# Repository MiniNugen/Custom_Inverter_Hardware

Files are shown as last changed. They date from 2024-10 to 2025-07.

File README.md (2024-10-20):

# Custom_Inverter_Hardware
## File Tree Should be organized like so:

PCB_Project_Name_REV1.PrjPCB  
|  Source Documents  
|  |  PCB_Project_Name_REV1.SchDOC  
|  |  PCB_Project_Name_REV1.PcbDOC  
|  |  BOM  
|  Settings  
|  Libraries  

PCB_Project_Name_REV2.PrjPCB  
|  Source Documents  
|  |  PCB_Project_Name_REV2.SchDOC  
|  |  PCB_Project_Name_REV2.PcbDOC  
|  |  BOM  
|  Settings  
|  Libraries  

PCB_Project_Name_REV3.PrjPCB  
|  Source Documents  
|  |  PCB_Project_Name_REV3.SchDOC  
|  |  PCB_Project_Name_REV3.PcbDOC  
|  |  BOM  
|  Settings  
|  Libraries

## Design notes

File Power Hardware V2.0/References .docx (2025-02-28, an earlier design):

https://www.ti.com/lit/ug/tiducg2/tiducg2.pdf

^main gate design reference

Gate driver ic data shee (https://www.ti.com/lit/ds/symlink/drv8300.pdf)t

Mosfet data sheet (https://www.ti.com/lit/ds/symlink/csd19532q5b.pdf?HQS=dis-dk-null-digikeymode-dsf-pf-null-wwe&ts=1740251644852)

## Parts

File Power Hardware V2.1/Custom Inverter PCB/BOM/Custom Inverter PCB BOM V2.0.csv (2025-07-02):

Reference | Value | Datasheet | Footprint | Qty | DNP | Part Number
C1,C15 | 0.1uF | https://www.digikey.ca/en/products/detail/kyocera-avx/0805ZD104KAT2A/1603455 | Capacitor_SMD:C_0805_2012Metric | 2 |  | 0805ZD104KAT2A
C2 | 0.33uF | https://www.digikey.ca/en/products/detail/murata-electronics/GRM219R71H334KA88D/702591 | Capacitor_SMD:C_0805_2012Metric | 1 |  | GRM219R71H334KA88D
C3,C4,C5 | 1uF | https://www.digikey.ca/en/products/detail/samsung-electro-mechanics/CL21B105KBFNFNE/3891014 | Capacitor_SMD:C_0805_2012Metric | 3 |  | CL21B105KBFNFNE
C6,C7,C8 | 1uF | https://www.digikey.ca/en/products/detail/tdk-corporation/CGA6M2X7R2A105K200AA/2443343 | Capacitor_SMD:C_1210_3225Metric | 3 |  | CGA6M2X7R2A105K200AA
C9,C10 | 330 µF | https://industrial.panasonic.com/cdbs/www-data/pdf/RDE0000/ABA0000C1181.pdf | EEV_FK2A331M:CAP_EEVFK2A331M | 2 |  | EEVFK2A331M
C11,C12,C13,C14 | 220nF | ~ | Capacitor_SMD:C_0603_1608Metric | 4 |  | CL21B224KAFNNNE
C21,C23,C24 | 47nF |  | Capacitor_SMD:C_0805_2012Metric | 3 |  | C0805C473K5RACTU
C28 | 0.1uF | https://www.digikey.ca/en/products/detail/yageo/CC0805KRX7R9BB104/302874 | Capacitor_SMD:C_0805_2012Metric | 1 |  | CC0805KRX7R9BB104
CR1,CR2,CR3 | ~ | BAV20WS-TP | BAV20WS-TP:CR_SOD-323_MCC | 3 |  | BAV20WS-TP
CR4 | LD1085D2M33R |  | LD1085D2M33R:D2PAK&slash_A_STM | 1 |  | LD1085D2M33R
F1,F2,F3,F4 | 250V 30A | 0463030.ER | 0463030_ER:FUSE_0463_LTF-M | 4 |  | 0463030.ER
J1,J2,J7,J8 | 1714971 |  | 1714971:PHOENIX_1714971 | 4 |  | 1714971
J3 | 1714968 |  | PHOENIX_1714968:PHOENIX_1714968 | 1 |  | 1714968
J4,J5,J9,J10 | 10897202 | 10897202 | CONN20_0010897202_MOL | 4 |  | 10897202
J6 | 1989764 | ~ | PHOENIX_1989764:PHOENIX_1989764 | 1 |  | 1989764
K2 | 1-1393210-3 |  | T9AS1D12_12:TE_1-1393210-3 | 1 |  | T9AS1D12-12
Q1,Q2,Q3,Q4,Q5,Q6 | CSD19532Q5B |  | CSD19532Q5B:TRANS_CSD19532Q5B | 6 |  | CSD19532Q5B
R1,R2,R3,R4,R6,R7 | 15R | https://www.digikey.ca/en/products/detail/panasonic-electronic-components/ERJ-6GEYJ150V/82975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 | Resistor_SMD:R_0805_2012Metric | 6 |  | ERJ-6GEYJ150V
R5,R8,R9,R18 | 10k | https://industrial.panasonic.com/cdbs/www-data/pdf/RDM0000/AOA0000C307.pdf | Resistor_SMD:R_0805_2012Metric | 4 |  | ERA-6AEB103V
R10,R11,R12,R13,R14,R15,R16,R17 | 4.7K | ~ | Resistor_SMD:R_0805_2012Metric | 8 |  | CRCW08054K70FKEAC
R32,R35,R36 | 220R |  | Resistor_SMD:R_0805_2012Metric | 3 |  | CRGCQ0805F220R
R43 | 97.6K | https://www.digikey.ca/en/products/detail/yageo/RC0805FR-0797K6L/728213 | Resistor_SMD:R_0805_2012Metric | 1 |  | RC0805FR-0797K6L
R44,R45,R46,R47,R48 | 3K | https://www.digikey.ca/en/products/detail/te-connectivity-passive-product/CRG0805F3K0/2380900 | Resistor_SMD:R_0805_2012Metric | 5 |  | CRG0805F3K0
TP1,TP2,TP3,TP4,TP5,TP6,TP7,TP8,TP9 | 5002 |  | 5002:KEYSTONE_5002 | 9 |  | 5002
U1 | DRV8300DIPWR | DRV8300DIPWR | DRV8300DIPWR:TSSOP_0DIPWR_TEX | 1 |  | DRV8300DIPWR
U2,U3,U4 | TLI4971A050T5E0001XUMA1 | TLI4971A050T5E0001XUMA1 | TLI4971A:IC_TLI4971A050T5UE0001XUMA1 | 3 |  | TLI4971A050T5E0001XUMA1
U5 | LAUNCHXL-F280049C |  | LAUNCHXL-F280049C:MODULE_LAUNCHXL-F280049C | 1 |  | LAUNCHXL-F280049C
U6 | OP292GSZ-REEL | OP292GSZ-REEL | R_8_ADI | 1 |  | OP292GSZ-REEL

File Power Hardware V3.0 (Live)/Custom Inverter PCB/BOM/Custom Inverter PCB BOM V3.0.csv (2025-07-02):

Reference | Value | Datasheet | Footprint | Qty | DNP | Part Number
C1,C2 | 330 µF | https://industrial.panasonic.com/cdbs/www-data/pdf/RDE0000/ABA0000C1181.pdf | EEV_FK2A331M:CAP_EEVFK2A331M | 2 |  | EEVFK2A331M
C3 | 0.1uF | https://www.digikey.ca/en/products/detail/yageo/CC0805KRX7R9BB104/302874 | Capacitor_SMD:C_0805_2012Metric | 1 |  | CC0805KRX7R9BB104
C4,C5,C6 | 1uF | https://www.digikey.ca/en/products/detail/samsung-electro-mechanics/CL21B105KBFNFNE/3891014 | Capacitor_SMD:C_0805_2012Metric | 3 |  | CL21B105KBFNFNE
C7,C8,C9 | 1uF | https://www.digikey.ca/en/products/detail/tdk-corporation/CGA6M2X7R2A105K200AA/2443343 | Capacitor_SMD:C_1210_3225Metric | 3 |  | CGA6M2X7R2A105K200AA
C10,C11,C12,C13,C27 | 220nF | ~ | Capacitor_SMD:C_0603_1608Metric | 5 |  | CL21B224KAFNNNE
C14,C15,C16 | 47nF |  | Capacitor_SMD:C_0805_2012Metric | 3 |  | C0805C473K5RACTU
C17,C24,C25 | 0.1uF | https://www.digikey.ca/en/products/detail/kyocera-avx/0805ZD104KAT2A/1603455 | Capacitor_SMD:C_0805_2012Metric | 3 |  | 0805ZD104KAT2A
C19,C20 | 0.33uF | https://www.digikey.ca/en/products/detail/murata-electronics/GRM219R71H334KA88D/702591 | Capacitor_SMD:C_0805_2012Metric | 2 |  | GRM219R71H334KA88D
CR1,CR2,CR3 | ~ | BAV20WS-TP | BAV20WS-TP:CR_SOD-323_MCC | 3 |  | BAV20WS-TP
CR4 | LD1085D2M33R | https://www.st.com/content/ccc/resource/technical/document/datasheet/d3/84/d5/f6/3c/23/40/7b/CD00001883.pdf/files/CD00001883.pdf/jcr:content/translations/en.C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 | LD1085D2M33R:D2PAK&slash_A_STM | 1 |  | LD1085D2M33R
D10,D11,D12,D13,D14 | 100V IN,12V,3.3V,5V,BRIDGE ON | https://mm.digikey.com/Volume0/opasdata/d220001/medias/docus/3739/B1931UY--20D000114U1930.pdf | Capacitor_SMD:C_0603_1608Metric_Pad1.08x0.95mm_HandSolder | 5 |  | B1931UY--20D000114U1930
F1,F2,F3,F4 | 100VDC 50A,250VAC 50A | https://www.bourns.com/docs/Product-Datasheets/SF-3812F-T.pdf | 0463030_ER:FUSE_0463_LTF-M | 4 |  | SF-3812F5000T-2
J1,J8,J9 | 1990009 |  | 2P term 1990009:PHOENIX_1990009 | 3 |  | 1990009
J2,J3,J4,J5 | 10897202 | 10897202 | CONN20_0010897202_MOL | 4 |  | 10897202
J6,J10,J11 | 1990041 |  | PHOENIX_1990041:PHOENIX_1990041 | 3 |  | 1990041
J7 | 1714971 |  | 1714971:PHOENIX_1714971 | 1 |  | 1714971
K1 | 1-1393210-3 | https://www.te.com/en/product-1-1393210-3.datasheet.pdf | T9AS1D12_12:TE_1-1393210-3 | 1 |  | 1-1393210-3
MP1,MP2,MP3,MP4,MP5 | 7461383 | 7461383 | M5 Screw Term 7461383:WP-SHFU_7461383 | 5 |  | 7461383
Q1,Q2,Q3,Q4,Q5,Q6 | IRFB4115PBF | https://www.infineon.com/dgdl/irfb4115pbf.pdf?fileId=5546d462533600a401535615ba6a1e0f | Package_TO_SOT_THT:TO-220-3_Vertical | 6 |  | IRFB4115PBF
R1 | 97.6K | https://www.digikey.ca/en/products/detail/yageo/RC0805FR-0797K6L/728213 | Resistor_SMD:R_0805_2012Metric | 1 |  | RC0805FR-0797K6L
R2,R22,R23,R26,R28 | 3K | https://www.digikey.ca/en/products/detail/te-connectivity-passive-product/CRG0805F3K0/2380900 | Resistor_SMD:R_0805_2012Metric | 5 |  | CRG0805F3K0
R3,R4,R5,R6,R7,R8 | 15R | https://www.digikey.ca/en/products/detail/panasonic-electronic-components/ERJ-6GEYJ150V/82975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 | Resistor_SMD:R_0805_2012Metric | 6 |  | ERJ-6GEYJ150V
R9,R10,R11,R12,R13,R14,R15,R16 | 4.7K | ~ | Resistor_SMD:R_0805_2012Metric | 8 |  | CRCW08054K70FKEAC
R17,R18,R19,R33,R34,R35,R36,R37 | 220R | CRGCQ0805F220R | Resistor_SMD:R_0805_2012Metric | 8 |  | CRGCQ0805F220R
R20 | 5.36k | https://www.yageo.com/upload/media/product/products/datasheet/rchip/PYu-RC_Group_51_RoHS_L_12.pdf | Resistor_SMD:R_0805_2012Metric | 1 |  | RC0805FR-075K36L
R21,R24,R25,R27 | 10k | https://industrial.panasonic.com/cdbs/www-data/pdf/RDM0000/AOA0000C307.pdf | Resistor_SMD:R_0805_2012Metric | 4 |  | ERA-6AEB103V
R49,R50,R51,R52 | 2.7k | https://industrial.panasonic.com/cdbs/www-data/pdf/RDO0000/AOA0000C331.pdf | Resistor_SMD:R_0805_2012Metric | 4 |  | ERJ-P06J272V
TP1,TP2,TP3,TP4,TP5,TP6,TP7,TP8,TP9 | 5002 |  | 5002:KEYSTONE_5002 | 9 |  | 5002
U1 | DRV8300DIPWR | https://www.ti.com/lit/ds/symlink/drv8300.pdf | DRV8300DIPWR:TSSOP_0DIPWR_TEX | 1 |  | DRV8300DIPWR
U2 | LAUNCHXL-F280049C | https://www.ti.com/lit/ug/spruii7b/spruii7b.pdf?ts=1748422871760 | LAUNCHXL-F280049C:MODULE_LAUNCHXL-F280049C | 1 |  | LAUNCHXL-F280049C
U3,U4,U5 | TLI4971A050T5E0001XUMA1 | https://www.infineon.com/dgdl/Infineon-TLI4971_25_50_75_120-DataSheet-v01_20-EN.pdf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 | TLI4971A:TLI4971A050T5UE0001XUMA1 | 3 |  | TLI4971A050T5E0001XUMA1
U6 | OP292GSZ-REEL | https://www.analog.com/media/en/technical-documentation/data-sheets/OP292_492.pdf | R_8_ADI | 1 |  | OP292GSZ-REEL
U7 | L78M05CDT-TR | L78M05CDT-TR | L78M05CDT_TR:DPAK_STM-M | 1 |  | L78M05CDT-TR

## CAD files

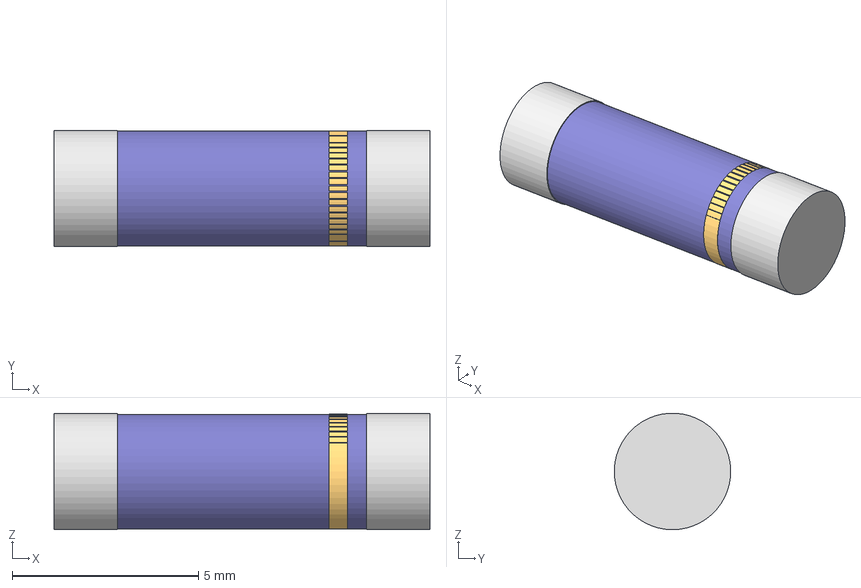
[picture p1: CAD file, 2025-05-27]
Power Hardware V3.0 (Live)/Custom Inverter PCB/EDA Models/0463030_ER/FUSE_0463_LTF.step
10.1 x 3.12 x 3.12 mm

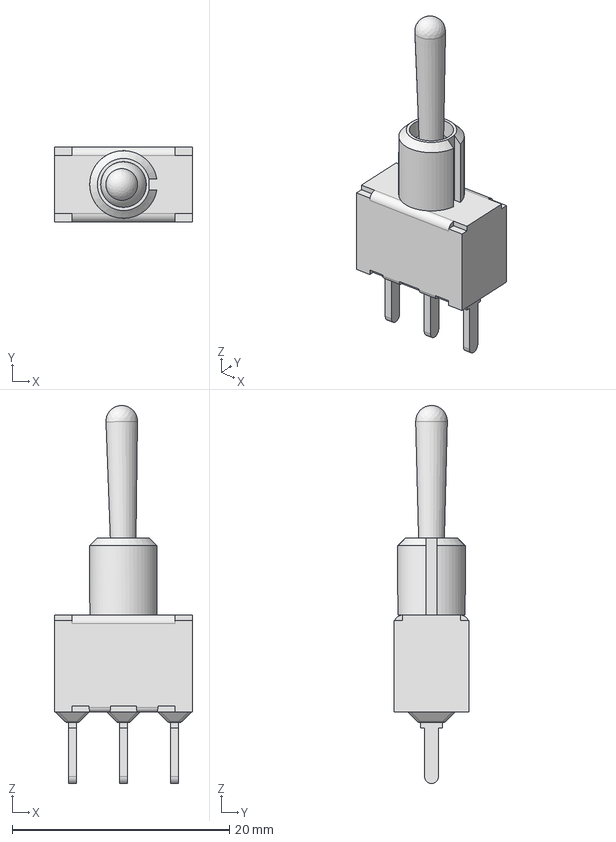
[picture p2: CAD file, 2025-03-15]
Power Hardware V3.0 (Live)/Custom Inverter PCB/EDA Models/100SP1T1B4M2QE/100SP1T1B4M2QE.step
12.7 x 6.86 x 34.8 mm

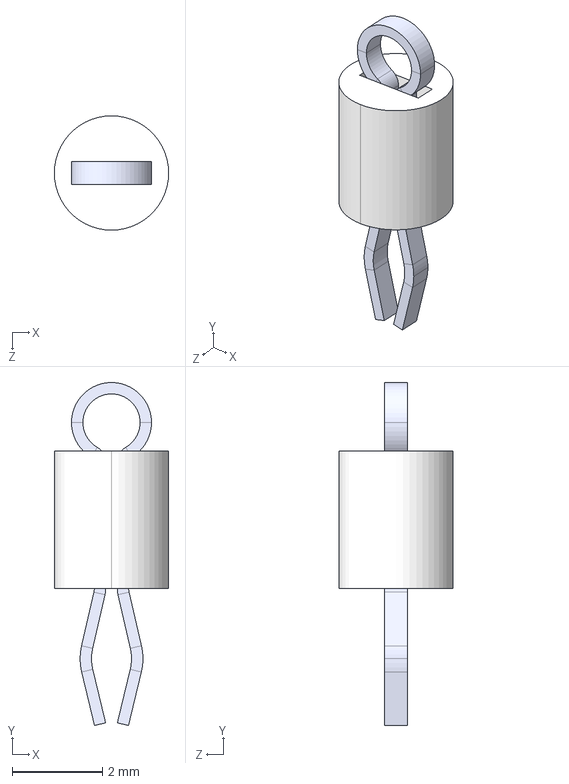
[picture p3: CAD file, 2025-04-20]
Power Hardware V3.0 (Live)/Custom Inverter PCB/EDA Models/5002/5002.step
2.54 x 7.62 x 2.54 mm

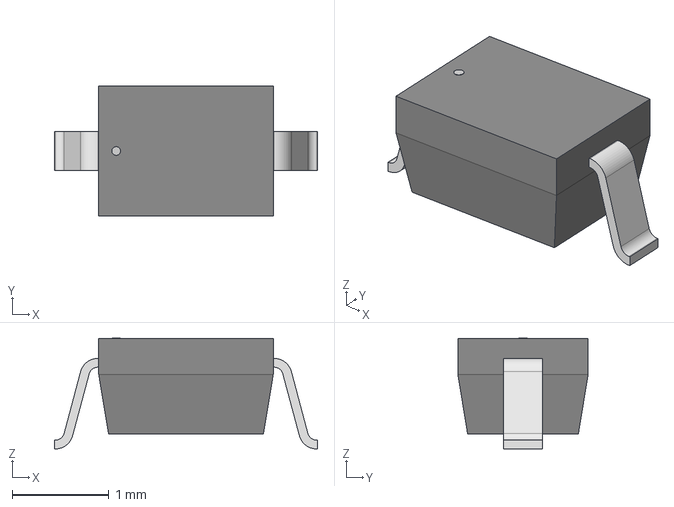
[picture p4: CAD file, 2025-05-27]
Power Hardware V3.0 (Live)/Custom Inverter PCB/EDA Models/BAV20WS_TP/CR_SOD-323_MCC.step
2.72 x 1.35 x 1.15 mm

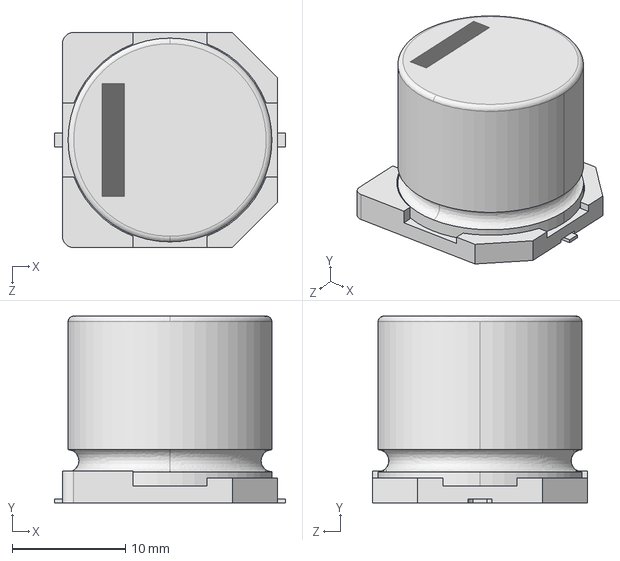
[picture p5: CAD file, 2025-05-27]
Power Hardware V3.0 (Live)/Custom Inverter PCB/EDA Models/EEV_FK2A331M/EEVFK2A331M.step
20.4 x 16.5 x 19.0 mm

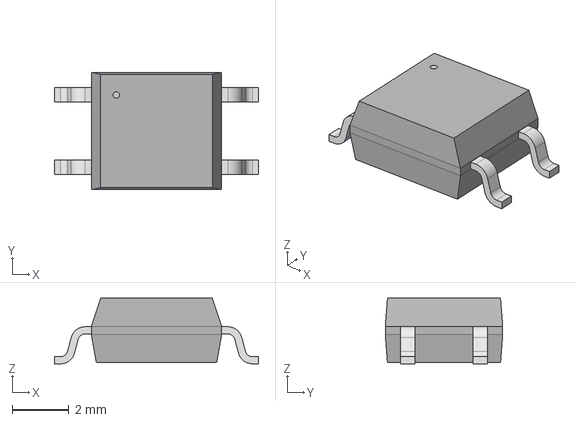
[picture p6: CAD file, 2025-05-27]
Power Hardware V3.0 (Live)/Custom Inverter PCB/EDA Models/HCPL_181_06BE/HCPL-181_BRA.step
7.19 x 4.14 x 2.31 mm

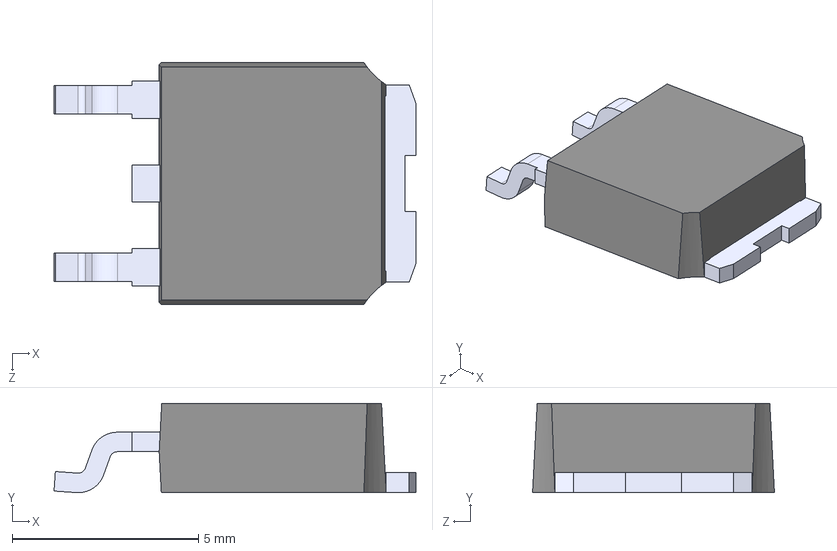
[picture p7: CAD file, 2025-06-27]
Power Hardware V3.0 (Live)/Custom Inverter PCB/EDA Models/L78M05CDT_TR/L78M05CDT-TR.step
9.72 x 2.40 x 6.50 mm

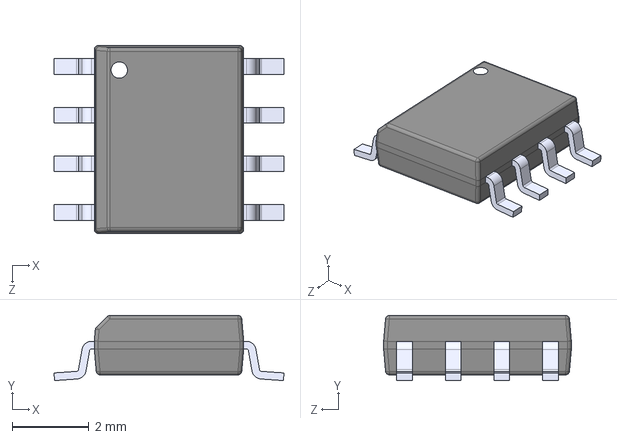
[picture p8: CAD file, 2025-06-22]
Power Hardware V3.0 (Live)/Custom Inverter PCB/EDA Models/LM5164DDAT/LM5164DDAT.step
6.00 x 1.70 x 4.90 mm

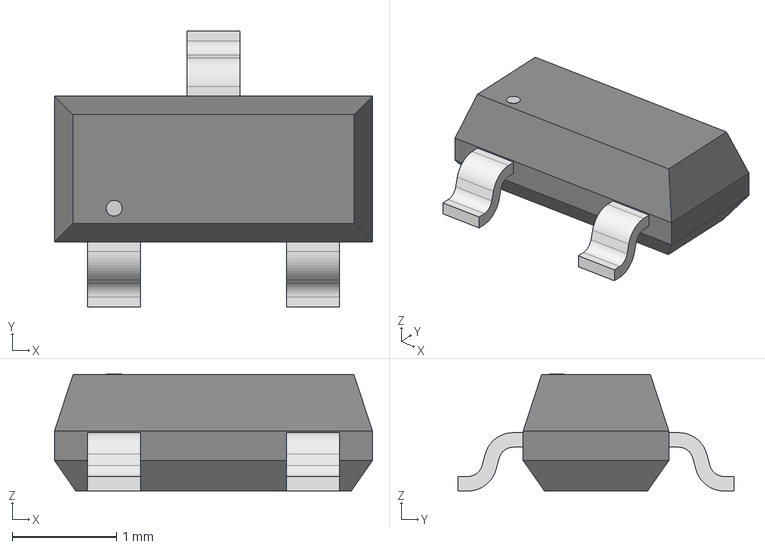
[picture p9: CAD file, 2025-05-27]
Power Hardware V3.0 (Live)/Custom Inverter PCB/EDA Models/NTR4170NT1G/SOT-23_ONS.step
3.05 x 2.64 x 1.12 mm

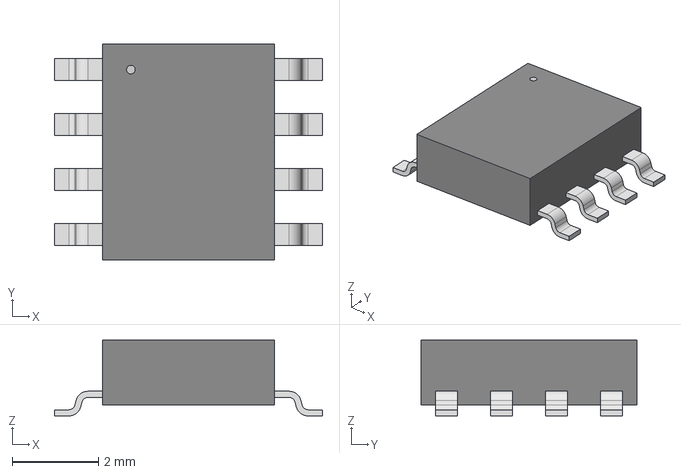
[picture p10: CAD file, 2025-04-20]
Power Hardware V3.0 (Live)/Custom Inverter PCB/EDA Models/OP292GSZ-REEL/OP292GSZ-REEL.step
6.20 x 5.00 x 1.75 mm

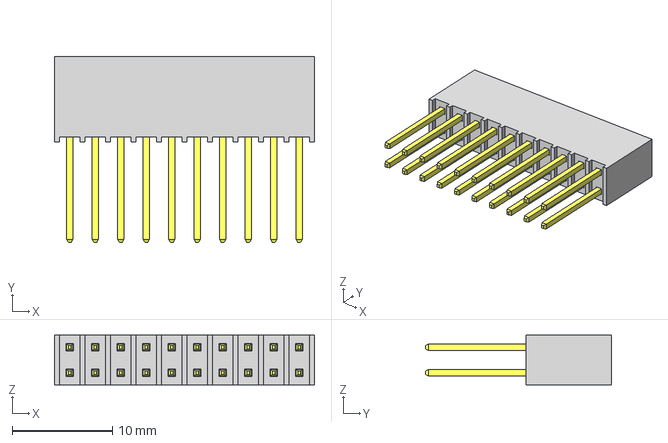
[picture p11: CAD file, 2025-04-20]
Power Hardware V3.0 (Live)/Custom Inverter PCB/EDA Models/SSQ_110_03_G_D/SSQ-110-03-G-D.step
25.9 x 18.5 x 4.95 mm
T1SSQ-110-03-G-D
P2SSQ-110-03-G-D

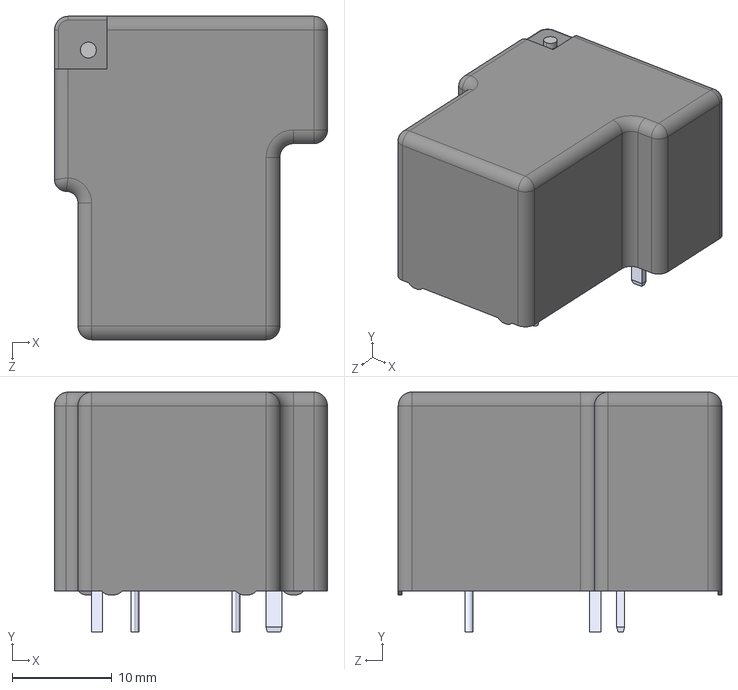
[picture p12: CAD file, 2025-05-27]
Power Hardware V3.0 (Live)/Custom Inverter PCB/EDA Models/T9AS1D12_12/1-1393210-3.step
27.4 x 24.1 x 32.5 mm

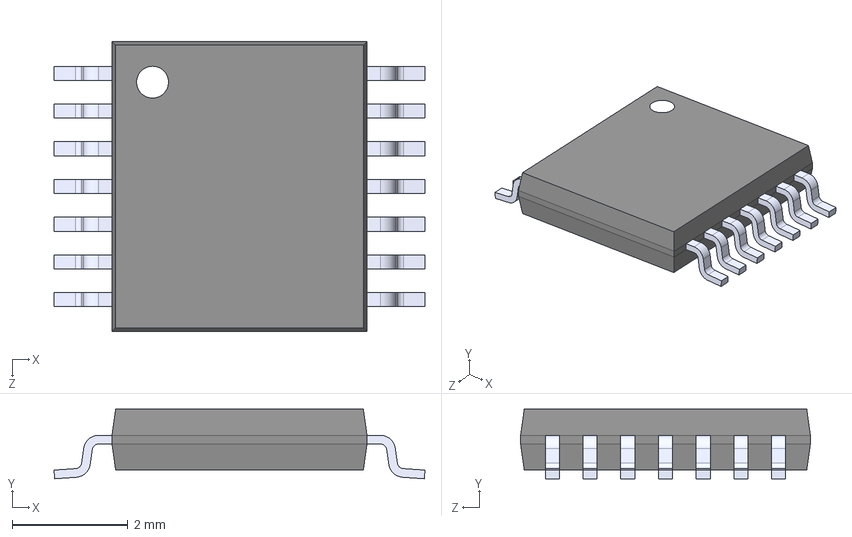
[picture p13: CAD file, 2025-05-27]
Power Hardware V3.0 (Live)/Custom Inverter PCB/EDA Models/TLV9004IPWR/TLV9004IPWR.step
6.40 x 1.20 x 5.00 mm

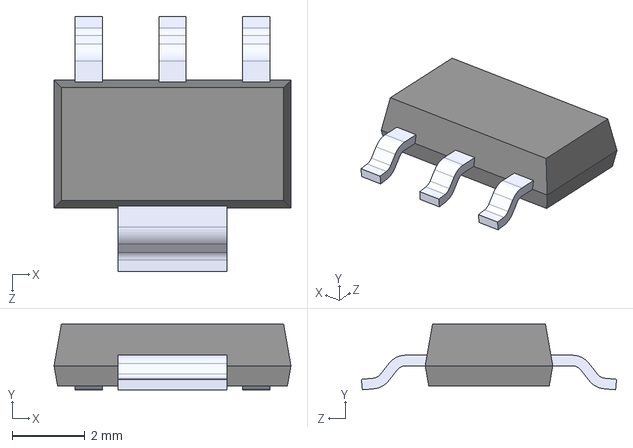
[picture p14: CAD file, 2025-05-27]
Power Hardware V3.0 (Live)/Custom Inverter PCB/EDA Models/UA78M33CDCYR/UA78M33CDCYR.step
6.50 x 1.80 x 7.00 mm

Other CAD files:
Power Hardware V3.0 (Live)/Custom Inverter PCB/EDA Models/1935161/1935161.step
Power Hardware V3.0 (Live)/Custom Inverter PCB/EDA Models/1989764/1989764.step
Power Hardware V3.0 (Live)/Custom Inverter PCB/EDA Models/1990041/1990041.step
Power Hardware V3.0 (Live)/Custom Inverter PCB/EDA Models/CSD19532Q5B/CSD19532Q5B.step
Power Hardware V2.0/LAUNCHXL-F280049C - ALTIUM/RevB/MCU025B_design_files/ALTIUM_EMBEDDED_MODELS/1051640001.stp
Power Hardware V2.0/LAUNCHXL-F280049C - ALTIUM/RevB/MCU025B_design_files/ALTIUM_EMBEDDED_MODELS/60900213421.stp
Power Hardware V2.0/LAUNCHXL-F280049C - ALTIUM/RevB/MCU025B_design_files/ALTIUM_EMBEDDED_MODELS/61300211121.stp
Power Hardware V2.0/LAUNCHXL-F280049C - ALTIUM/RevB/MCU025B_design_files/ALTIUM_EMBEDDED_MODELS/61300311121.stp
Power Hardware V2.0/LAUNCHXL-F280049C - ALTIUM/RevB/MCU025B_design_files/ALTIUM_EMBEDDED_MODELS/D0008A.stp
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

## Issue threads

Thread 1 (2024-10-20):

Select test motor that the inverter will be made to test

MiniNugen, 2024-10-20:
Decide on a motor so we can design our project around it.
Requirements:
- 3-Phase AC
- Permanent-magnet synchronous motor
- 60V to 120V AC voltage
- No larger than 8kW of power draw

Closed 2024-10-26.

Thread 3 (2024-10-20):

Simulate a 3-phase H Bridge + PWM current generator

MiniNugen, 2024-10-20:
A PWM controller is required to drive a 3-phase H-bridge setup. When done correctly, the output of each inverter phase should have a voltage level proportional to the duty cycle of the PWM controller.

[This model is what my our inverter will be based on. So read this if you need extra resources](https://uwin365-my.sharepoint.com/:b:/g/personal/nguyen39_uwindsor_ca/EXIsp8yUNkpArx_SbNmMhxcB7SE95WXn12xlHMAQ0pFSlA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)

TLDR: Here's the plan, we'll need  3 PWM controllers. One for each phase. They will each receive an analog signal input between 2 to 12V. A 2V signal means the PWM is getting requested to generate a 0% duty cycle wave and a 12V means the PWM is getting requested to generate a 100% duty cycle wave. The wave will have ____Hz frequency (We'll decide on a frequency after we've established a speed requirement).  These PWM signals will be used to drive a Transistor array. Then the PWM signal is at 0% duty cycle, we should expect to see 0V at the output of that H-Bridge phase, When the PWM signal is at 100%, we should see our Power voltage at the output.

When the Duty cycle is 0%, we would expect the overall voltage at that phase to be 0%

Josh-Levesque, 2024-10-22:
[This model is what my our inverter will be based on. So read this if you need extra resources](https://uwin365-my.sharepoint.com/:b:/r/personal/nguyen39_uwindsor_ca/Documents/%5BFULLTEXT01.pdf%5D(https://uwin365-my.sharepoint.com/:b:/r/personal/nguyen39_uwindsor_ca/Documents/FULLTEXT01.pdf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)?csf=1&web=1&e=icIfjU)

This link is broken

Closed 2024-10-26.

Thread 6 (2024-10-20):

First Iteration of controls circuit.

MiniNugen, 2024-10-20:
Design, the first Iteration of the control board.
Just a fast microprocessor that needs to work fast to keep up with calculating PARK and CLARKE conversions, track current data, receive Throttle inputs, and perform traction control. This also needs some built-in PI and PID controllers.

Closed 2025-01-09.

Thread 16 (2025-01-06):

Revision2 Hardware Design

MiniNugen, 2025-01-06:
Revision 2 is where the gate driver circuit and microcontroller circuit are put together into 1 PCB.
Some updates for this revision shoud include:
- replace all passive components smaller than 0603. This is to make manufacturing easier.
- Reduce the microcontroller board down to 4 layers
- Conjoin both gate driver board and micro controller circuit.
- Remove all unused GPIO connections

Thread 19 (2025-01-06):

Copy the current microcontroller and Gate Driver PCB into one shared altiumproject

MiniNugen, 2025-01-06:
After converting the microcontroller PCB from 6 layers to a 4-layer board, it shall be inspected and approved.
Copy the modified microcontroller and the latest Gate Driver PCB into one shared Altium project (file name: TI-C200 inverter V2)

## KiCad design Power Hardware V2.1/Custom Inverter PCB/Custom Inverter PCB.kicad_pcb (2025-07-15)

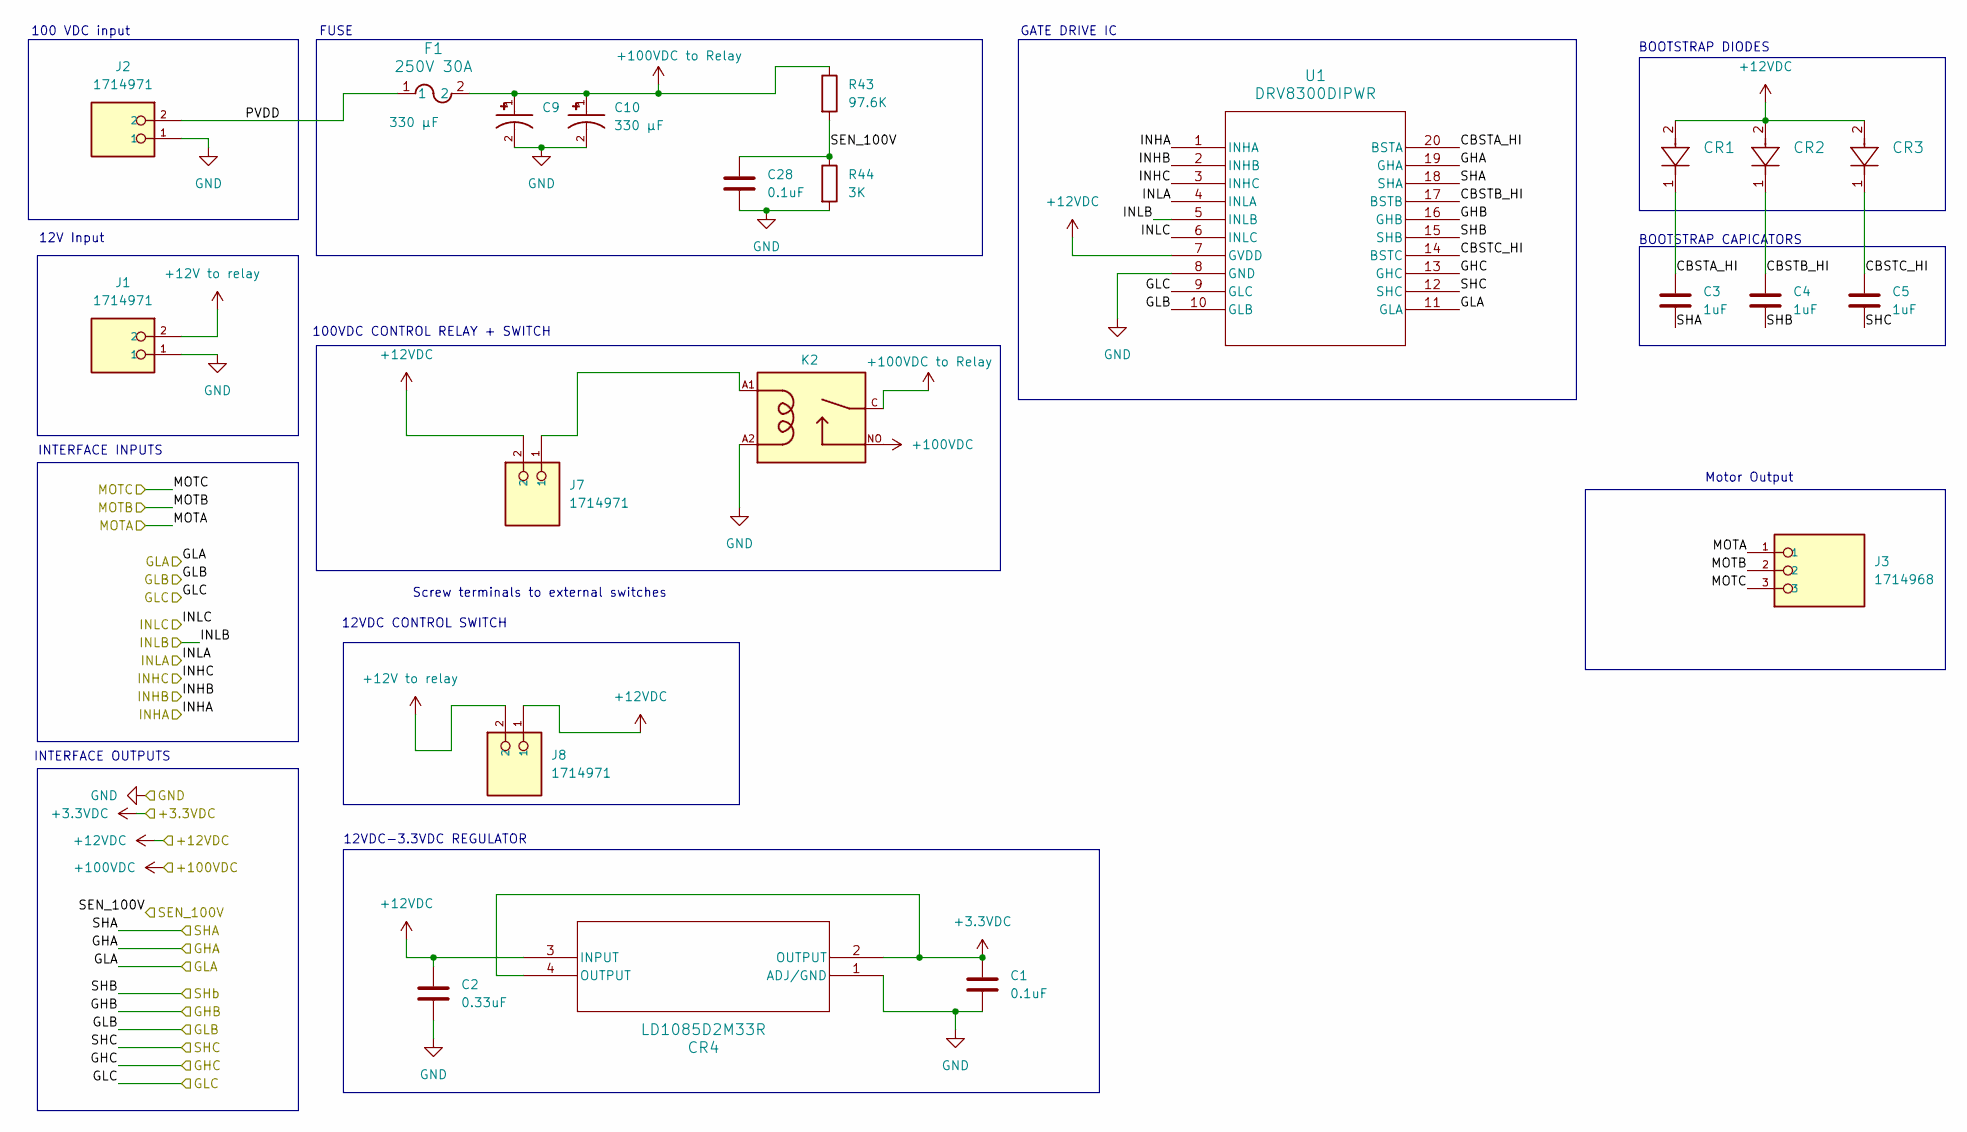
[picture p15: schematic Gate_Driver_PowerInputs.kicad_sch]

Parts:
C1: 0.1uF; C_0805_2012Metric; Part Number 0805ZD104KAT2A
C2: 0.33uF; C_0805_2012Metric; Part Number GRM219R71H334KA88D
C3, C4, C5: 1uF; C_0805_2012Metric; Part Number CL21B105KBFNFNE
C9, C10: 330 µF; CAP_EEVFK2A331M; PARTREV 10-Oct-19
C28: 0.1uF; C_0805_2012Metric; Part Number CC0805KRX7R9BB104
CR1, CR2, CR3: CR_SOD-323_MCC; Part Number BAV20WS-TP
CR4: LD1085D2M33R; D2PAK&slash_A_STM; Part Number LD1085D2M33R
F1: 250V 30A; FUSE_0463_LTF-M; Part Number 0463030.ER
J1, J2, J7, J8: 1714971; PHOENIX_1714971; PARTREV 26.05.2020
J3: 1714968; PHOENIX_1714968; Part Number 1714968
K2: 1-1393210-3; TE_1-1393210-3; PARTREV 0815
R43: 97.6K; R_0805_2012Metric; Part Number RC0805FR-0797K6L
R44: 3K; R_0805_2012Metric; Part Number CRG0805F3K0
U1: DRV8300DIPWR; TSSOP_0DIPWR_TEX; Part Number DRV8300DIPWR

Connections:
+3.3V: C1.1, CR4.2 (OUTPUT), CR4.4 (OUTPUT); also elsewhere on the board
+12V to relay: J1.2, J8.2
+12VDC: C2.1, CR1.2, CR2.2, CR3.2, CR4.3 (INPUT), J7.2, J8.1, U1.7 (GVDD)
+100VDC: K2.NO; also elsewhere on the board
+100VDC to Relay: C9.1, C10.1, F1.2, K2.C, R43.1
/GateDriver&Power Inputs/CBSTA_HI: C3.1, CR1.1, U1.20 (BSTA)
/GateDriver&Power Inputs/CBSTB_HI: C4.1, CR2.1, U1.17 (BSTB)
/GateDriver&Power Inputs/CBSTC_HI: C5.1, CR3.1, U1.14 (BSTC)
/GateDriver&Power Inputs/GHA: U1.19 (GHA); also elsewhere on the board
/GateDriver&Power Inputs/GHB: U1.16 (GHB); also elsewhere on the board
/GateDriver&Power Inputs/GHC: U1.13 (GHC); also elsewhere on the board
/GateDriver&Power Inputs/GLA: U1.11 (GLA); also elsewhere on the board
/GateDriver&Power Inputs/GLB: U1.10 (GLB); also elsewhere on the board
/GateDriver&Power Inputs/GLC: U1.9 (GLC); also elsewhere on the board
/GateDriver&Power Inputs/PVDD: F1.1, J2.2
/INHA: U1.1 (INHA); also elsewhere on the board
/INHB: U1.2 (INHB); also elsewhere on the board
/INHC: U1.3 (INHC); also elsewhere on the board
/INLA: U1.4 (INLA); also elsewhere on the board
/INLB: U1.5 (INLB); also elsewhere on the board
/INLC: U1.6 (INLC); also elsewhere on the board
/MOTA: J3.1; also elsewhere on the board
/MOTB: J3.2; also elsewhere on the board
/MOTC: J3.3; also elsewhere on the board
/SEN_100V: C28.1, R43.2, R44.1; also elsewhere on the board
/SHA: C3.2, U1.18 (SHA); also elsewhere on the board
/SHB: C4.2, U1.15 (SHB); also elsewhere on the board
/SHC: C5.2, U1.12 (SHC); also elsewhere on the board
GND: C1.2, C2.2, C9.2, C10.2, C28.2, CR4.1 (ADJ/GND), J1.1, J2.1, K2.A2, R44.2, U1.8 (GND); also elsewhere on the board
unnamed: J7.1, K2.A1

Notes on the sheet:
100VDC CONTROL RELAY + SWITCH
Motor Output
100 VDC input
12VDC-3.3VDC REGULATOR
12V Input
Screw terminals to external switches
FUSE
12VDC CONTROL SWITCH
GATE DRIVE IC
INTERFACE INPUTS
BOOTSTRAP DIODES
BOOTSTRAP CAPICATORS
INTERFACE OUTPUTS

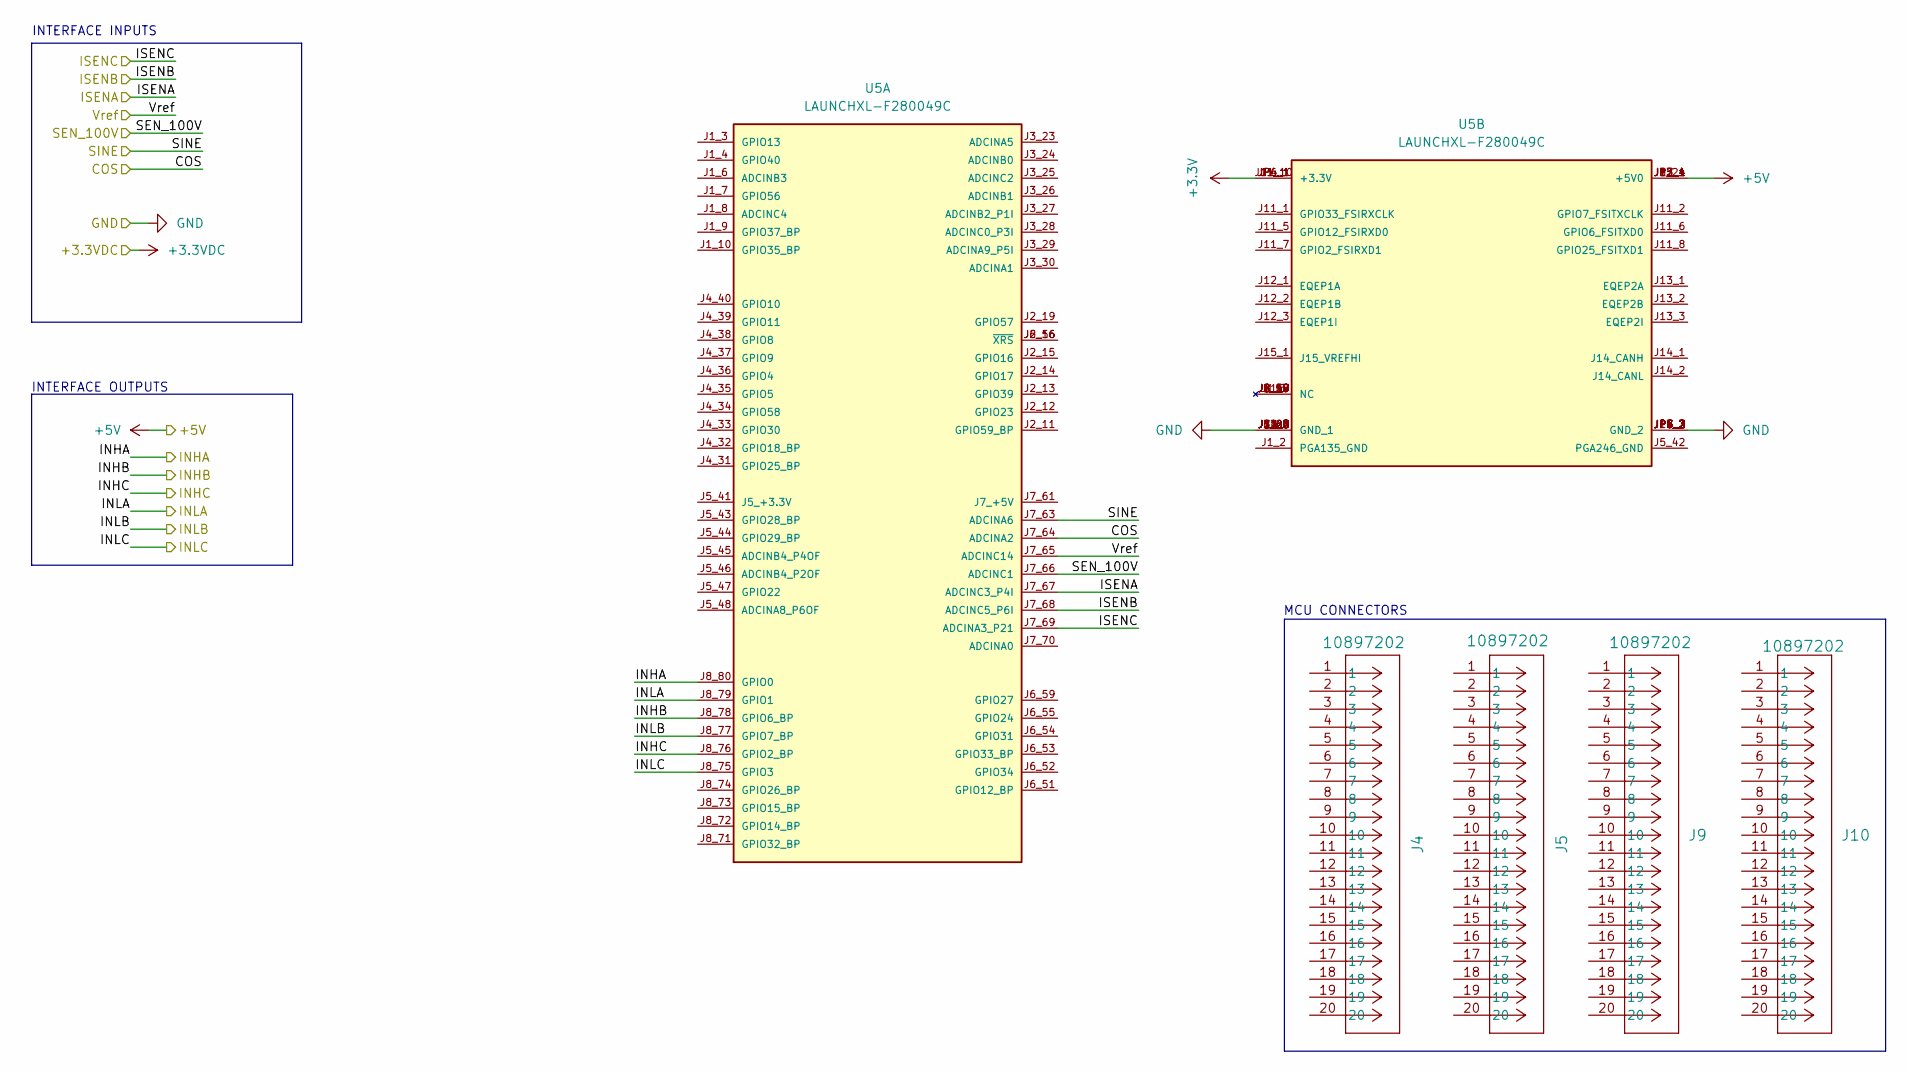
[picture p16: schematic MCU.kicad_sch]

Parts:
J4, J5, J9, J10: 10897202; CONN20_0010897202_MOL; Part Number 10897202
U5: LAUNCHXL-F280049C; MODULE_LAUNCHXL-F280049C; PARTREV B

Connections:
+3.3V: U5.J1_1 (+3.3V), U5.J11_10 (+3.3V), U5.JP4_1 (+3.3V), U5.JP6_1 (+3.3V); also elsewhere on the board
+5V: U5.J3_21 (+5V0), U5.J12_4 (+5V0), U5.J13_4 (+5V0), U5.JP5_1 (+5V0), U5.JP7_1 (+5V0); also elsewhere on the board
/Current sense/ISENA: U5.J7_67 (ADCINC3_P4I); also elsewhere on the board
/Current sense/ISENB: U5.J7_68 (ADCINC5_P6I); also elsewhere on the board
/Current sense/ISENC: U5.J7_69 (ADCINA3_P21); also elsewhere on the board
/Current sense/Vref: U5.J7_65 (ADCINC14); also elsewhere on the board
/Encoder Input/COS_MCU: U5.J7_64 (ADCINA2); also elsewhere on the board
/Encoder Input/SIN_MCU: U5.J7_63 (ADCINA6); also elsewhere on the board
/INHA: U5.J8_80 (GPIO0); also elsewhere on the board
/INHB: U5.J8_78 (GPIO6_BP); also elsewhere on the board
/INHC: U5.J8_76 (GPIO2_BP); also elsewhere on the board
/INLA: U5.J8_79 (GPIO1); also elsewhere on the board
/INLB: U5.J8_77 (GPIO7_BP); also elsewhere on the board
/INLC: U5.J8_75 (GPIO3); also elsewhere on the board
/SEN_100V: U5.J7_66 (ADCINC1); also elsewhere on the board
GND: U5.J2_20 (GND_1), U5.J3_22 (GND_1), U5.J6_60 (GND_1), U5.J7_62 (GND_1), U5.J11_3 (GND_1), U5.J11_4 (GND_1), U5.J12_5 (GND_1), U5.J13_5 (GND_1), U5.J14_3 (GND_1), U5.J15_2 (GND_2), U5.JP4_2 (GND_2), U5.JP4_3 (GND_2), U5.JP5_2 (GND_2), U5.JP5_3 (GND_2), U5.JP6_2 (GND_2), U5.JP6_3 (GND_2), U5.JP7_2 (GND_2), U5.JP7_3 (GND_2); also elsewhere on the board
unnamed: U5.J2_16 (~XRS), U5.J6_56 (~XRS)

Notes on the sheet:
INTERFACE INPUTS
INTERFACE OUTPUTS
MCU CONNECTORS

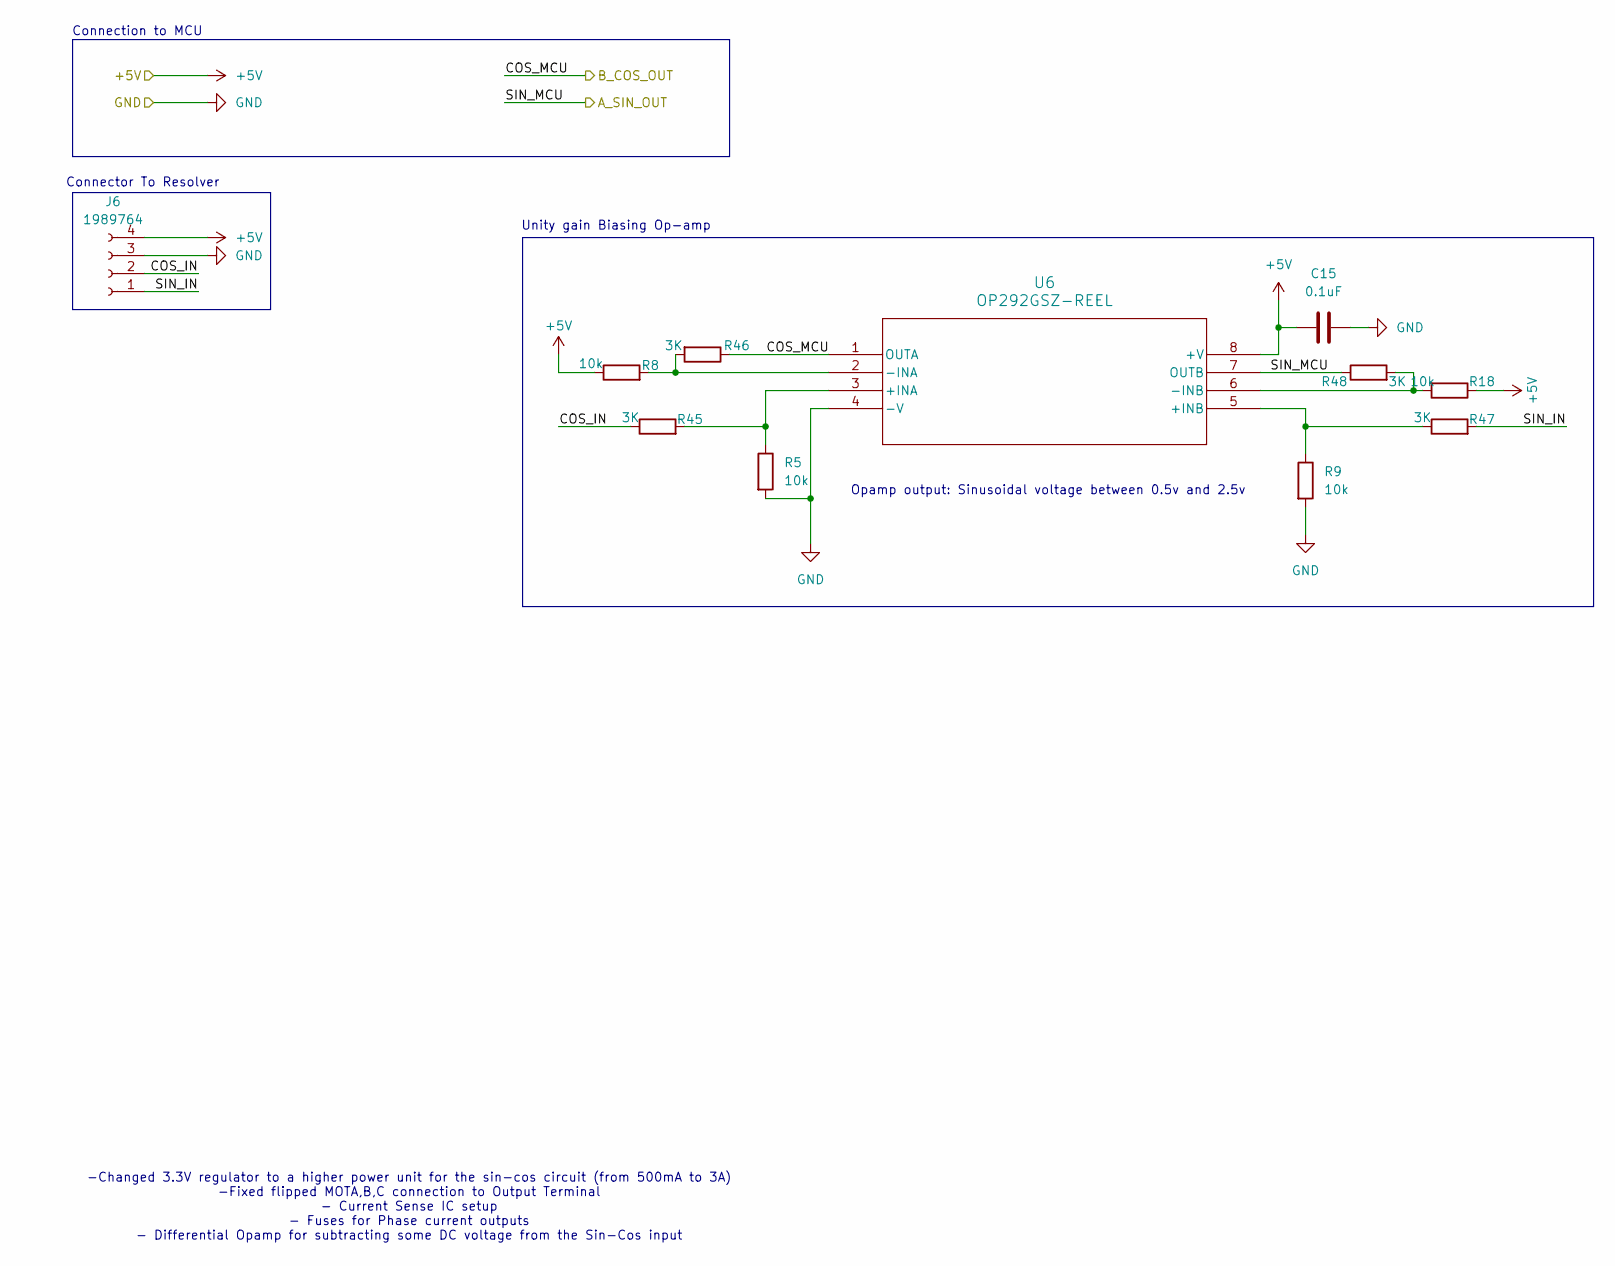
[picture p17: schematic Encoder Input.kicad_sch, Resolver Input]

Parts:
C15: 0.1uF; C_0805_2012Metric; Part Number 0805ZD104KAT2A
J6: 1989764; PHOENIX_1989764
R5, R9, R18: 10k; R_0805_2012Metric; Part Number ERA-6AEB103V
R8: 10k; R_0805_2012Metric
R45, R46, R47, R48: 3K; R_0805_2012Metric; Part Number CRG0805F3K0
U6: OP292GSZ-REEL; R_8_ADI

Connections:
+5V: C15.1, J6.4, R8.1, R18.1, U6.8 (+V); also elsewhere on the board
/Encoder Input/COS_IN: J6.2, R45.1
/Encoder Input/COS_MCU: R46.1, U6.1 (OUTA); also elsewhere on the board
/Encoder Input/SIN_IN: J6.1, R47.2
/Encoder Input/SIN_MCU: R48.1, U6.7 (OUTB); also elsewhere on the board
GND: C15.2, J6.3, R5.2, R9.2, U6.4 (-V); also elsewhere on the board
unnamed: R5.1, R45.2, U6.3 (+INA)
unnamed: R9.1, R47.1, U6.5 (+INB)
unnamed: R8.2, R46.2, U6.2 (-INA)
unnamed: R18.2, R48.2, U6.6 (-INB)

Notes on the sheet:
Opamp output: Sinusoidal voltage between 0.5v and 2.5v
Connector To Resolver
Unity gain Biasing Op-amp
-Changed 3.3V regulator to a higher power unit for the sin-cos circuit (from 500mA to 3A) -Fixed flipped MOTA,B,C connection to Output Terminal - Current Sense IC setup - Fuses for Phase current outputs - Differential Opamp for subtracting some DC voltage from the Sin-Cos input
Connection to MCU

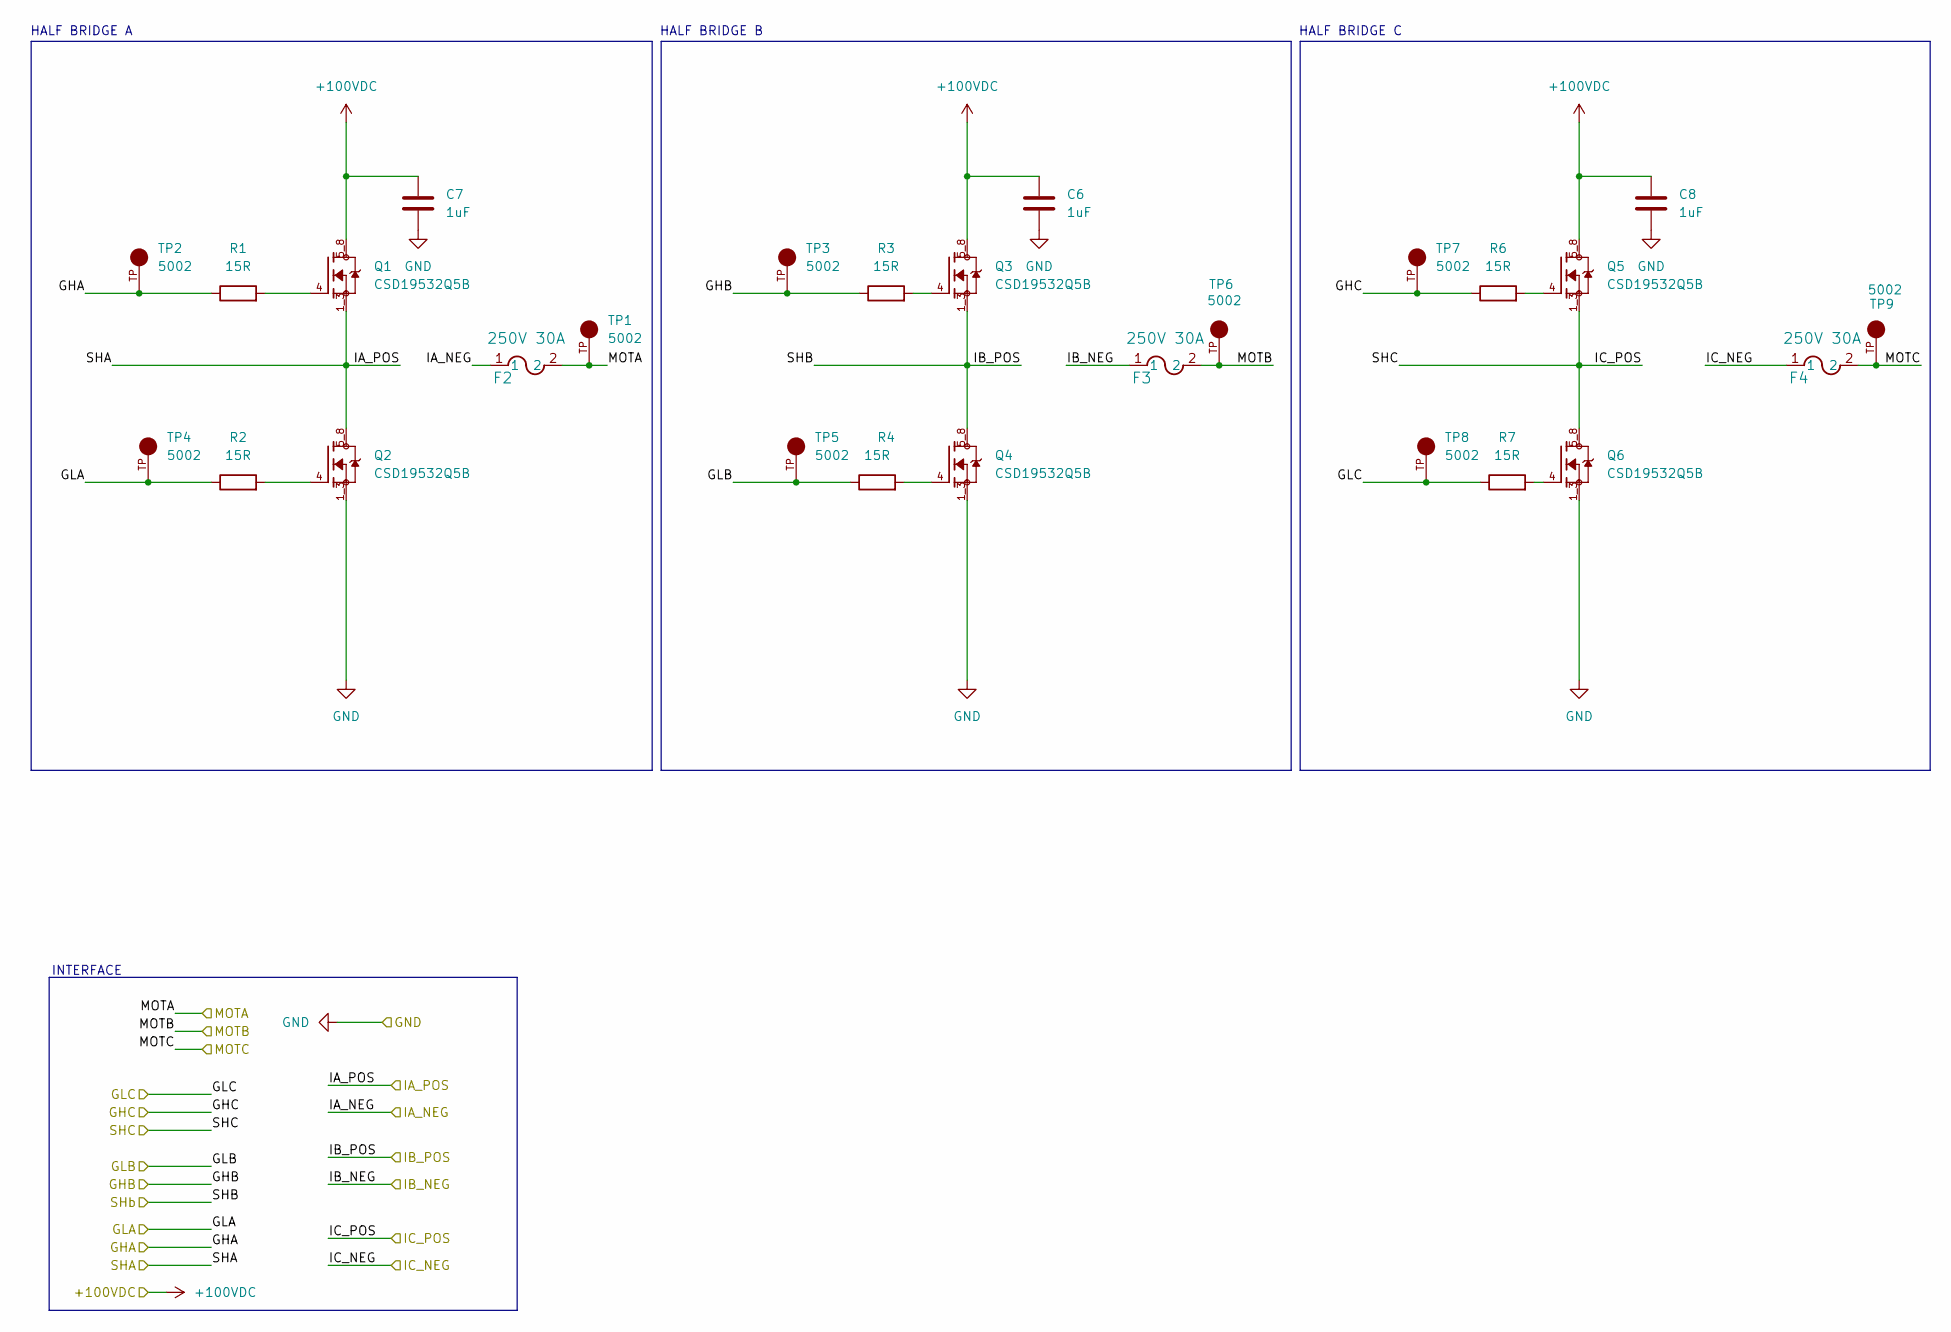
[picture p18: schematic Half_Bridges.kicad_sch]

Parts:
C6, C7, C8: 1uF; C_1210_3225Metric; Part Number CGA6M2X7R2A105K200AA
F2, F3, F4: 250V 30A; FUSE_0463_LTF-M; Part Number 0463030.ER
Q1, Q2, Q3, Q4, Q5, Q6: CSD19532Q5B; TRANS_CSD19532Q5B; PARTREV B
R1, R2, R3, R4, R6, R7: 15R; R_0805_2012Metric; Part Number ERJ-6GEYJ150V
TP1, TP2, TP3, TP4, TP5, TP6, TP7, TP8, TP9: 5002; KEYSTONE_5002; PARTREV H

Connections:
+100VDC: C6.1, C7.1, C8.1, Q1.5_8, Q3.5_8, Q5.5_8; also elsewhere on the board
/Current sense/IA-: F2.1; also elsewhere on the board
/Current sense/IB-: F3.1; also elsewhere on the board
/Current sense/IC-: F4.1; also elsewhere on the board
/GateDriver&Power Inputs/GHA: R1.1, TP2.TP; also elsewhere on the board
/GateDriver&Power Inputs/GHB: R3.1, TP3.TP; also elsewhere on the board
/GateDriver&Power Inputs/GHC: R6.1, TP7.TP; also elsewhere on the board
/GateDriver&Power Inputs/GLA: R2.1, TP4.TP; also elsewhere on the board
/GateDriver&Power Inputs/GLB: R4.1, TP5.TP; also elsewhere on the board
/GateDriver&Power Inputs/GLC: R7.1, TP8.TP; also elsewhere on the board
/MOTA: F2.2, TP1.TP; also elsewhere on the board
/MOTB: F3.2, TP6.TP; also elsewhere on the board
/MOTC: F4.2, TP9.TP; also elsewhere on the board
/SHA: Q1.1_3, Q2.5_8; also elsewhere on the board
/SHB: Q3.1_3, Q4.5_8; also elsewhere on the board
/SHC: Q5.1_3, Q6.5_8; also elsewhere on the board
GND: C6.2, C7.2, C8.2, Q2.1_3, Q4.1_3, Q6.1_3; also elsewhere on the board
unnamed: Q1.4, R1.2
unnamed: Q2.4, R2.2
unnamed: Q3.4, R3.2
unnamed: Q4.4, R4.2
unnamed: Q5.4, R6.2
unnamed: Q6.4, R7.2

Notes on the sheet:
HALF BRIDGE B
HALF BRIDGE A
INTERFACE
HALF BRIDGE C

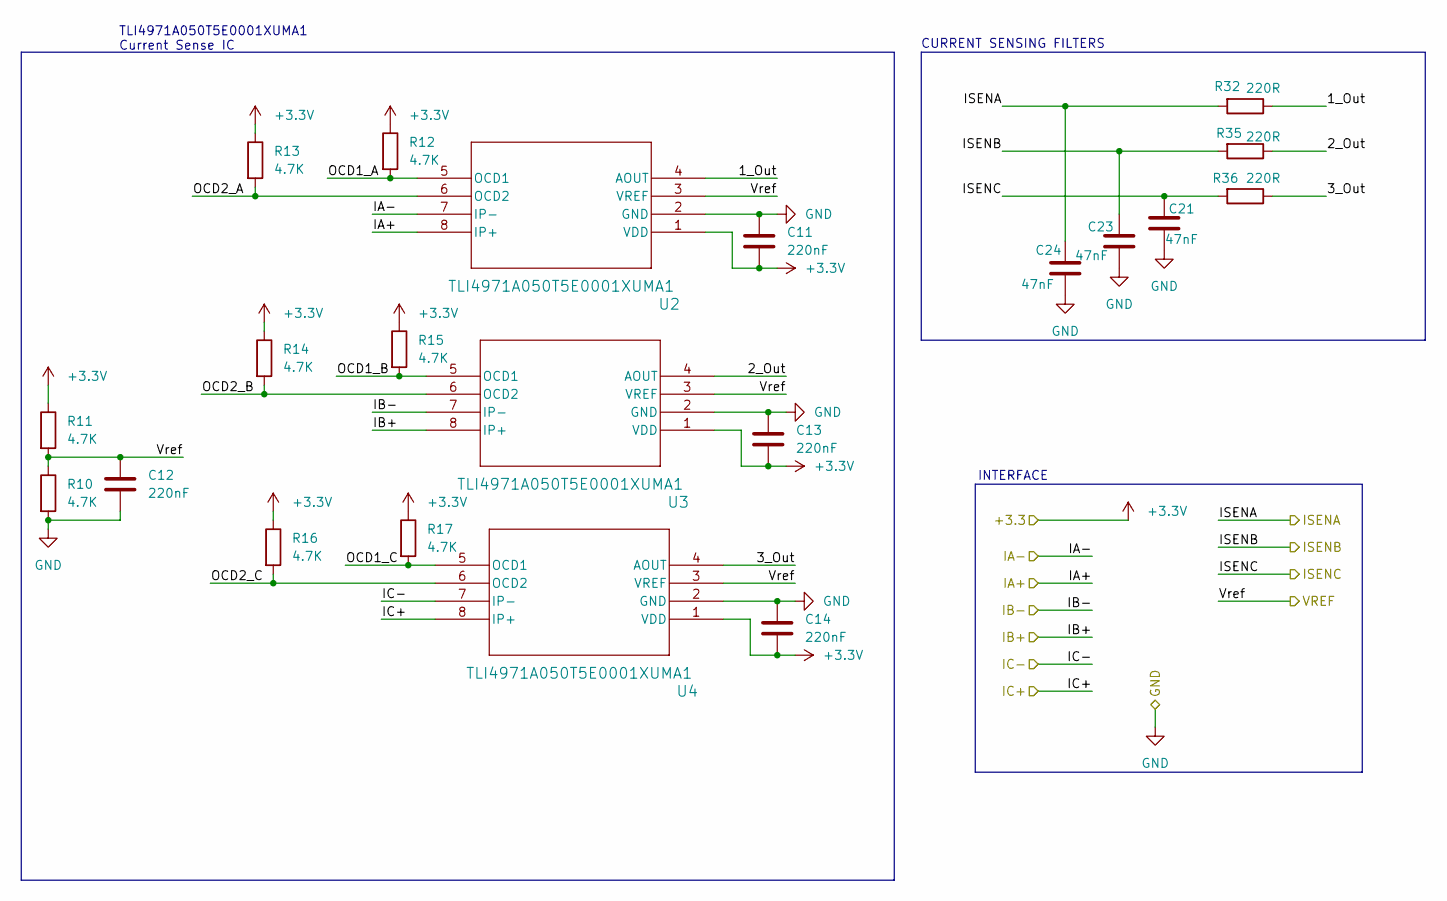
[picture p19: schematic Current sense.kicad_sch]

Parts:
C11, C12, C13, C14: 220nF; C_0603_1608Metric; Part Number CL21B224KAFNNNE
C21, C23, C24: 47nF; C_0805_2012Metric; Part Number C0805C473K5RACTU
R10, R11, R12, R13, R14, R15, R16, R17: 4.7K; R_0805_2012Metric; Part Number CRCW08054K70FKEAC
R32, R35, R36: 220R; R_0805_2012Metric; Part Number CRGCQ0805F220R
U2, U3, U4: TLI4971A050T5E0001XUMA1; IC_TLI4971A050T5UE0001XUMA1; Part Number TLI4971A050T5E0001XUMA1

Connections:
+3.3V: C11.2, C13.2, C14.2, R11.1, R12.1, R13.1, R14.1, R15.1, R16.1, R17.1, U2.1 (VDD), U3.1 (VDD), U4.1 (VDD); also elsewhere on the board
/Current sense/1_Out: R32.1, U2.4 (AOUT)
/Current sense/2_Out: R35.1, U3.4 (AOUT)
/Current sense/3_Out: R36.1, U4.4 (AOUT)
/Current sense/IA-: U2.7 (IP-); also elsewhere on the board
/Current sense/IB-: U3.7 (IP-); also elsewhere on the board
/Current sense/IC-: U4.7 (IP-); also elsewhere on the board
/Current sense/ISENA: C24.1, R32.2; also elsewhere on the board
/Current sense/ISENB: C23.1, R35.2; also elsewhere on the board
/Current sense/ISENC: C21.1, R36.2; also elsewhere on the board
/Current sense/OCD1_A: R12.2, U2.5 (OCD1)
/Current sense/OCD1_B: R15.2, U3.5 (OCD1)
/Current sense/OCD1_C: R17.2, U4.5 (OCD1)
/Current sense/OCD2_A: R13.2, U2.6 (OCD2)
/Current sense/OCD2_B: R14.2, U3.6 (OCD2)
/Current sense/OCD2_C: R16.2, U4.6 (OCD2)
/Current sense/Vref: C12.1, R10.1, R11.2, U2.3 (VREF), U3.3 (VREF), U4.3 (VREF); also elsewhere on the board
/SHA: U2.8 (IP+); also elsewhere on the board
/SHB: U3.8 (IP+); also elsewhere on the board
/SHC: U4.8 (IP+); also elsewhere on the board
GND: C11.1, C12.2, C13.1, C14.1, C21.2, C23.2, C24.2, R10.2, U2.2 (GND), U3.2 (GND), U4.2 (GND); also elsewhere on the board

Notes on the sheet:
CURRENT SENSING FILTERS
INTERFACE
TLI4971A050T5E0001XUMA1 Current Sense IC

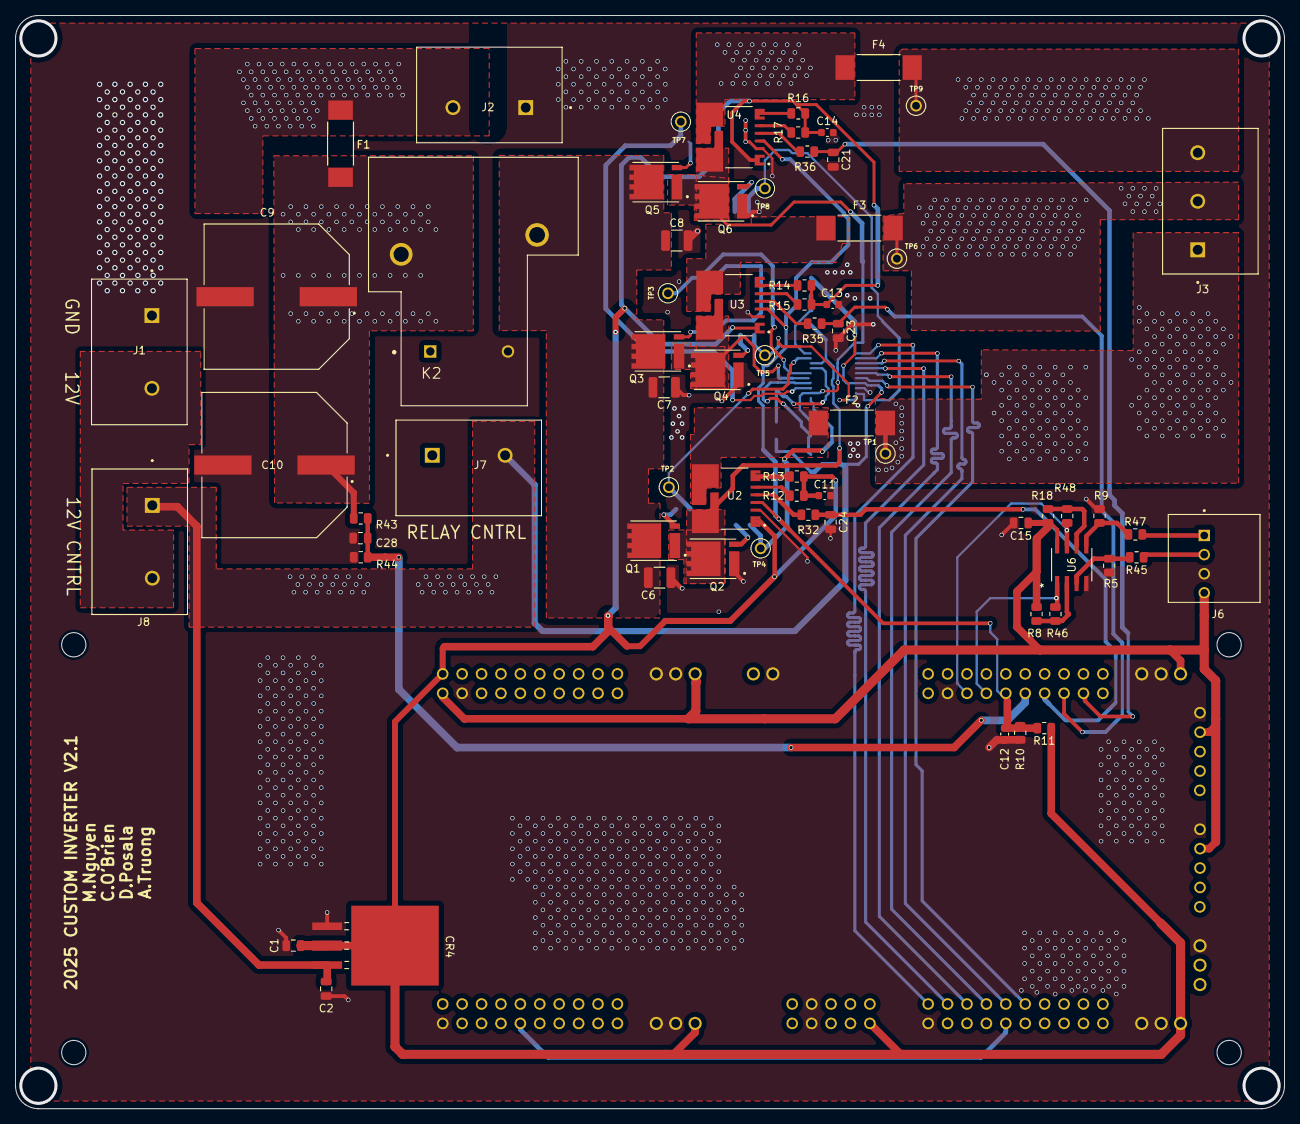
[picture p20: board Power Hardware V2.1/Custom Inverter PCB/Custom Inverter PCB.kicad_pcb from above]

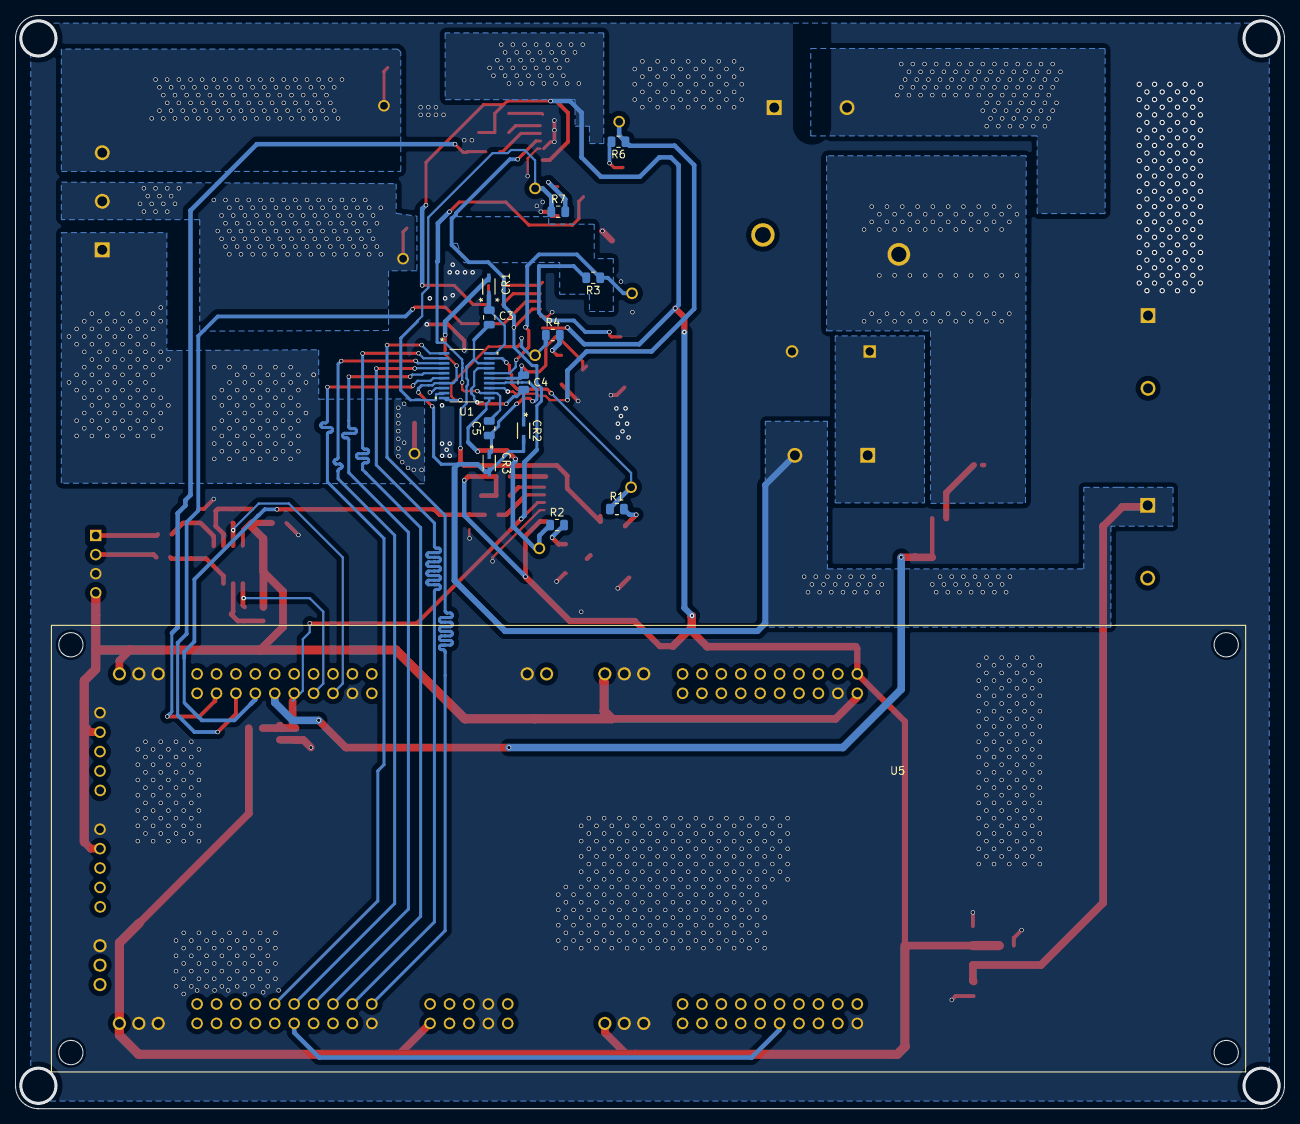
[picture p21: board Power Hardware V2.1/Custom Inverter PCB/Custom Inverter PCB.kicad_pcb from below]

Board: 2 copper layers, 166.0 x 143.0 mm, 82 parts (14 on the bottom side), 62 nets.

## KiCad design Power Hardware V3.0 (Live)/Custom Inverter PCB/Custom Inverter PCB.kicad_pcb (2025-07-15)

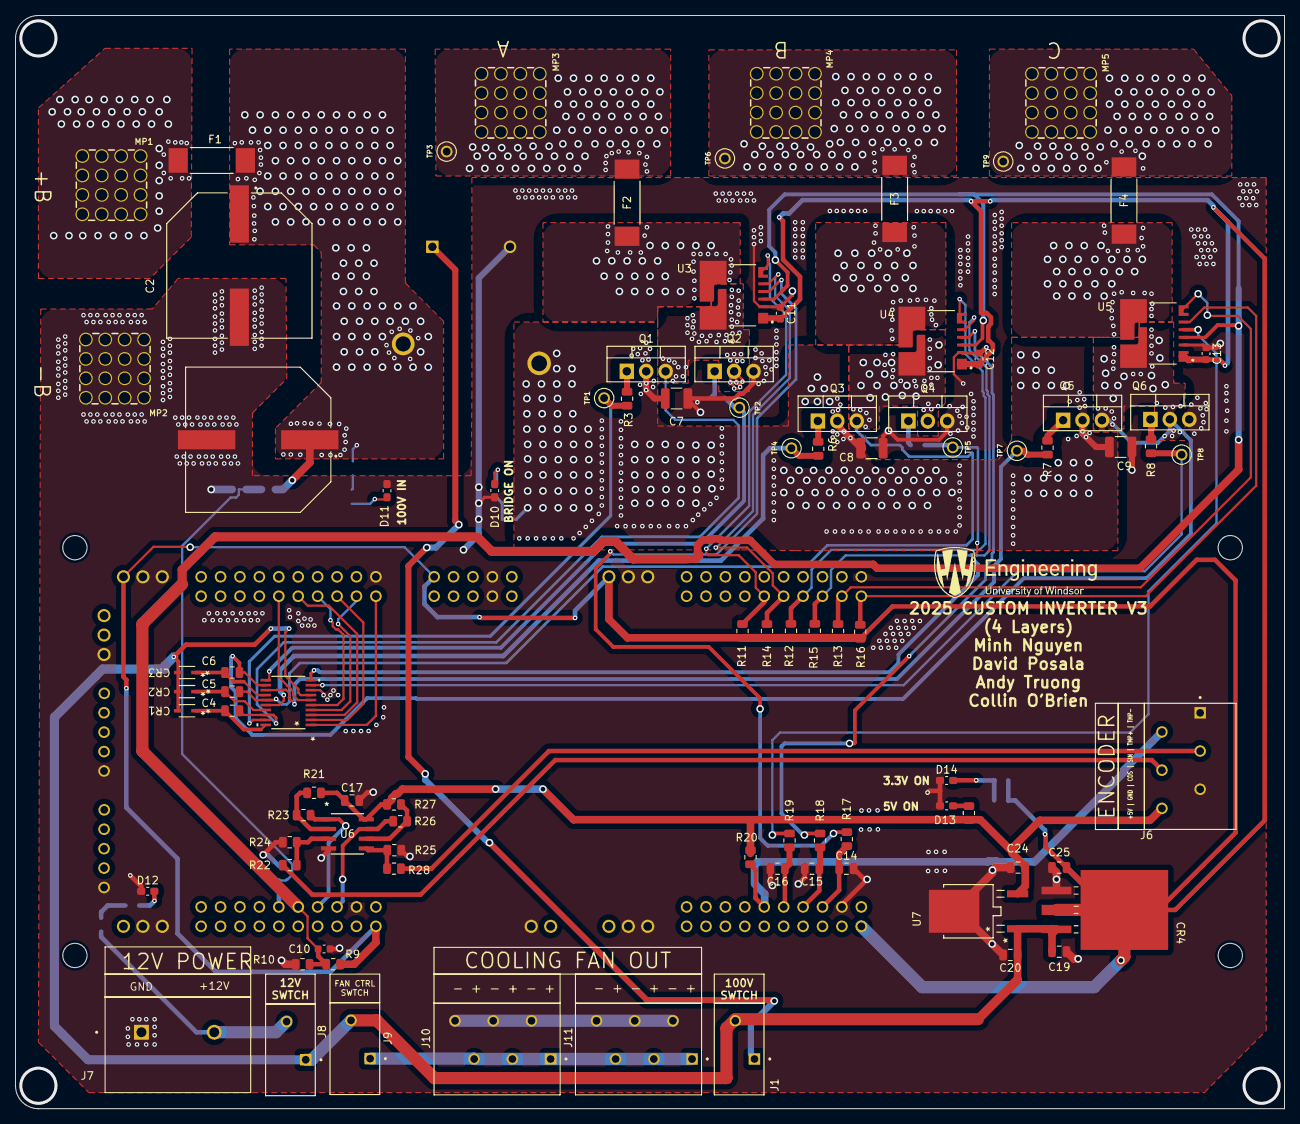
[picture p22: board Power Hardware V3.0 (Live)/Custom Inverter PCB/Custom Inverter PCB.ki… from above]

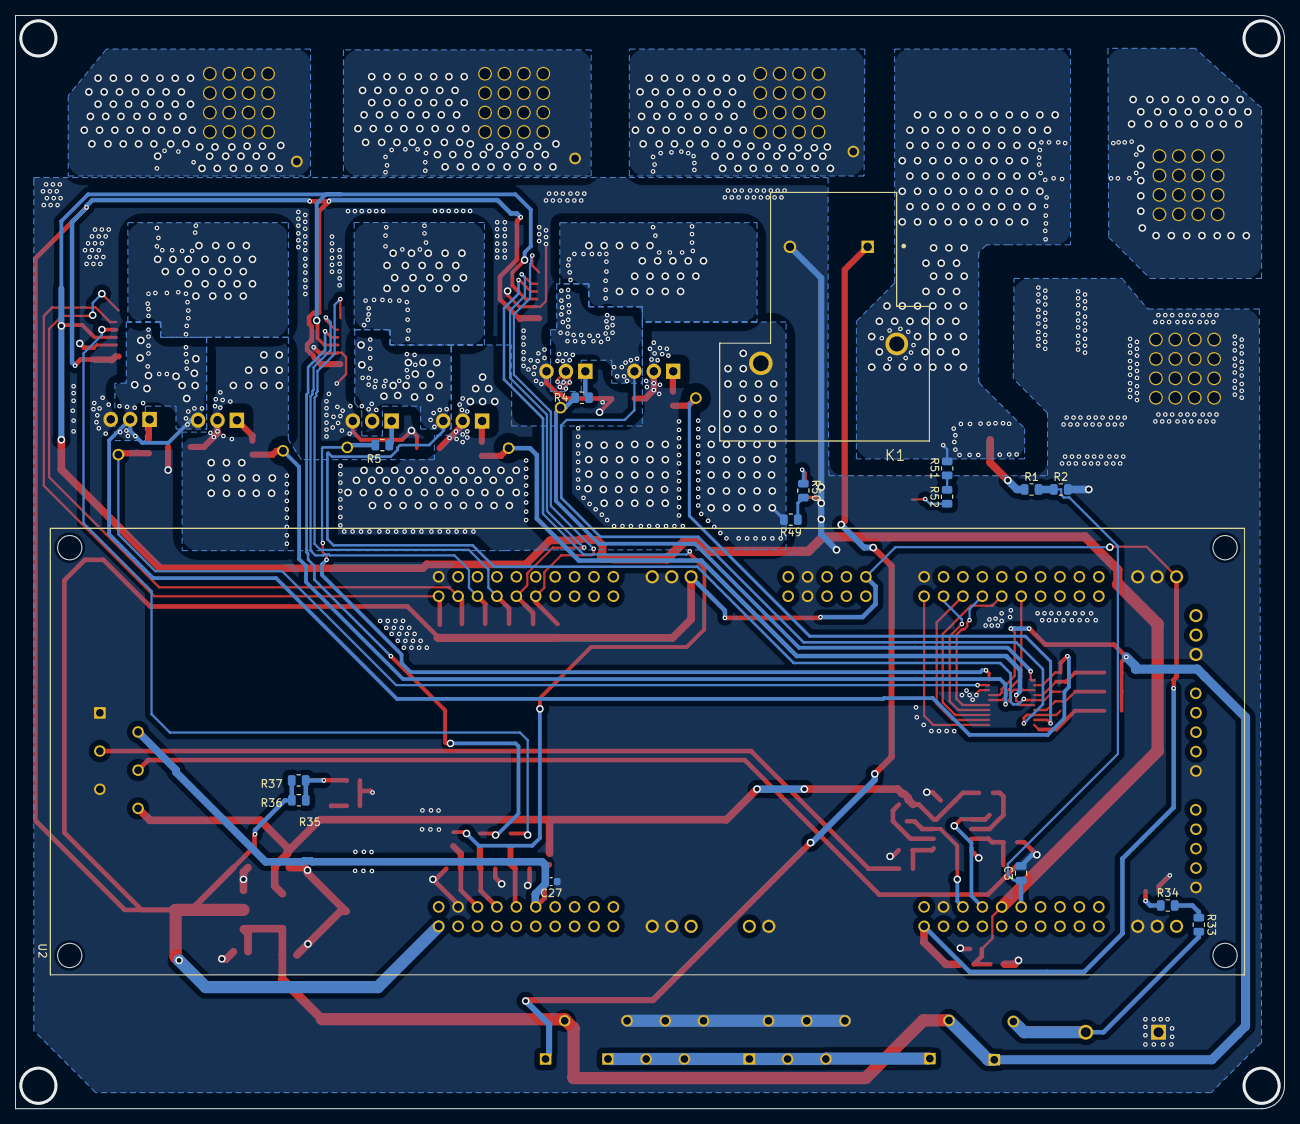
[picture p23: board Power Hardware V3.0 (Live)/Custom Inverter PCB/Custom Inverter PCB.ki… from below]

Board: 4 copper layers, 166.0 x 143.0 mm, 107 parts (16 on the bottom side), 71 nets.

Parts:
C1, C2: 330 µF; CAP_EEVFK2A331M
C3, C17, C24, C25: 0.1uF; C_0805_2012Metric
C4, C5, C6: 1uF; C_0805_2012Metric
C7, C8, C9: 1uF; C_1210_3225Metric
C10, C11, C12, C13, C27: 220nF; C_0603_1608Metric
C14, C15, C16: 47nF; C_0805_2012Metric
C19, C20: 0.33uF; C_0805_2012Metric
CR1, CR2, CR3: CR_SOD-323_MCC
CR4: LD1085D2M33R; D2PAK&slash_A_STM
D10: BRIDGE ON; C_0603_1608Metric_Pad1.08x0.95mm_HandSolder
D11: 100V IN; C_0603_1608Metric_Pad1.08x0.95mm_HandSolder
D12: 12V; C_0603_1608Metric_Pad1.08x0.95mm_HandSolder
D13: 5V; C_0603_1608Metric_Pad1.08x0.95mm_HandSolder
D14: 3.3V; C_0603_1608Metric_Pad1.08x0.95mm_HandSolder
F1: 100VDC 50A; FUSE_0463_LTF-M
F2, F3, F4: 250VAC 50A; FUSE_0463_LTF-M
J1, J8, J9: 1990009; PHOENIX_1990009
J6, J10, J11: 1990041; PHOENIX_1990041
J7: 1714971; PHOENIX_1714971
K1: 1-1393210-3; TE_1-1393210-3
MP1, MP2, MP3, MP4, MP5: 7461383; WP-SHFU_7461383
Q1, Q2, Q3, Q4, Q5, Q6: IRFB4115PBF; TO-220-3_Vertical
R1: 97.6K; R_0805_2012Metric
R2, R22, R23, R26, R28: 3K; R_0805_2012Metric
R3, R4, R5, R6, R7, R8: 15R; R_0805_2012Metric
R9, R10, R11, R12, R13, R14, R15, R16: 4.7K; R_0805_2012Metric
R17, R18, R19, R33, R34, R35, R36, R37: 220R; R_0805_2012Metric
R20: 5.36k; R_0805_2012Metric
R21, R24, R25, R27: 10k; R_0805_2012Metric
R49, R50, R51, R52: 2.7k; R_0805_2012Metric
TP1, TP2, TP3, TP4, TP5, TP6, TP7, TP8, TP9: 5002; KEYSTONE_5002
U1: DRV8300DIPWR; TSSOP_0DIPWR_TEX
U2: LAUNCHXL-F280049C; MODULE_LAUNCHXL-F280049C
U3, U4, U5: TLI4971A050T5E0001XUMA1; TLI4971A050T5UE0001XUMA1
U6: OP292GSZ-REEL; R_8_ADI
U7: L78M05CDT-TR; DPAK_STM-M

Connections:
+3.3VDC: C11.2, C12.2, C13.2, C25.1, CR4.2 (OUTPUT), CR4.4 (OUTPUT), R9.1, R11.1, R12.1, R13.1, R14.1, R15.1, R16.1, R36.2, R37.2, U2.J1_1 (+3.3V), U2.J5_41 (J5_+3.3V), U2.J11_10 (+3.3V), U2.JP4_1 (+3.3V), U2.JP6_1 (+3.3V), U3.1 (VDD), U4.1 (VDD), U5.1 (VDD)
+5V: C17.1, C24.1, J6.6, R20.2, R21.1, R27.1, R35.2, U6.8 (+V), U7.2 (OUTPUT)
+12V to relay: J7.2, J8.2, R33.2
+12VDC: C19.1, C20.1, CR1.2, CR2.2, CR3.2, CR4.3 (INPUT), J1.2, J8.1, J9.2, U1.7 (GVDD), U7.1 (INPUT)
+100VDC: C7.1, C8.1, C9.1, K1.NO, Q1.2 (D), Q3.2 (D), Q5.2 (D), R49.2
+100VDC to Relay: C1.1, C2.1, F1.2, K1.C, R1.1, R51.2
/Current sense/1_Out: R17.1, U3.4 (AOUT)
/Current sense/2_Out: R18.1, U4.4 (AOUT)
/Current sense/3_Out: R19.1, U5.4 (AOUT)
/Current sense/IA-: F2.1, U3.7 (IP-)
/Current sense/IB-: F3.1, U4.7 (IP-)
/Current sense/IC-: F4.1, U5.7 (IP-)
/Current sense/ISENA: C14.1, R17.2, U2.J3_23 (ADCINA5)
/Current sense/ISENB: C15.1, R18.2, U2.J3_24 (ADCINB0)
/Current sense/ISENC: C16.1, R19.2, U2.J3_25 (ADCINC2)
/Current sense/OCD1_A: R14.2, U2.J4_36 (GPIO4), U3.5 (OCD1)
/Current sense/OCD1_B: R15.2, U2.J4_38 (GPIO8), U4.5 (OCD1)
/Current sense/OCD1_C: R16.2, U2.J4_40 (GPIO10), U5.5 (OCD1)
/Current sense/OCD2_A: R11.2, U2.J4_35 (GPIO5), U3.6 (OCD2)
/Current sense/OCD2_B: R12.2, U2.J4_37 (GPIO9), U4.6 (OCD2)
/Current sense/OCD2_C: R13.2, U2.J4_39 (GPIO11), U5.6 (OCD2)
/Current sense/Vref: C10.1, R9.2, R10.1, U2.J7_65 (ADCINC14), U3.3 (VREF), U4.3 (VREF), U5.3 (VREF)
/Encoder Input/COS_IN: J6.4, R22.1
/Encoder Input/COS_MCU: R23.1, U2.J7_64 (ADCINA2), U6.1 (OUTA)
/Encoder Input/SIN_IN: J6.3, R28.2
/Encoder Input/SIN_MCU: R26.1, U2.J7_63 (ADCINA6), U6.7 (OUTB)
/Encoder Input/Temp+: C27.1, J6.2, R20.1, U2.J3_26 (ADCINB1)
/GateDriver&Power Inputs/CBSTA_HI: C4.1, CR1.1, U1.20 (BSTA)
/GateDriver&Power Inputs/CBSTB_HI: C5.1, CR2.1, U1.17 (BSTB)
/GateDriver&Power Inputs/CBSTC_HI: C6.1, CR3.1, U1.14 (BSTC)
/GateDriver&Power Inputs/GHA: R3.1, TP1.TP, U1.19 (GHA)
/GateDriver&Power Inputs/GHB: R6.1, TP4.TP, U1.16 (GHB)
/GateDriver&Power Inputs/GHC: R7.1, TP7.TP, U1.13 (GHC)
/GateDriver&Power Inputs/GLA: R4.1, TP2.TP, U1.11 (GLA)
/GateDriver&Power Inputs/GLB: R5.1, TP5.TP, U1.10 (GLB)
/GateDriver&Power Inputs/GLC: R8.1, TP8.TP, U1.9 (GLC)
/GateDriver&Power Inputs/PVDD: F1.1, MP1.1, MP1.2, MP1.3, MP1.4, MP1.5, MP1.6, MP1.7, MP1.8, MP1.9, MP1.10, MP1.11, MP1.12, MP1.13, MP1.14, MP1.15, MP1.16
/INHA: U1.1 (INHA), U2.J8_80 (GPIO0)
/INHB: U1.2 (INHB), U2.J8_78 (GPIO6_BP)
/INHC: U1.3 (INHC), U2.J8_76 (GPIO2_BP)
/INLA: U1.4 (INLA), U2.J8_79 (GPIO1)
/INLB: U1.5 (INLB), U2.J8_77 (GPIO7_BP)
/INLC: U1.6 (INLC), U2.J8_75 (GPIO3)
/MOTA: F2.2, MP3.1, MP3.2, MP3.3, MP3.4, MP3.5, MP3.6, MP3.7, MP3.8, MP3.9, MP3.10, MP3.11, MP3.12, MP3.13, MP3.14, MP3.15, MP3.16, TP3.TP
/MOTB: F3.2, MP4.1, MP4.2, MP4.3, MP4.4, MP4.5, MP4.6, MP4.7, MP4.8, MP4.9, MP4.10, MP4.11, MP4.12, MP4.13, MP4.14, MP4.15, MP4.16, TP6.TP
/MOTC: F4.2, MP5.1, MP5.2, MP5.3, MP5.4, MP5.5, MP5.6, MP5.7, MP5.8, MP5.9, MP5.10, MP5.11, MP5.12, MP5.13, MP5.14, MP5.15, MP5.16, TP9.TP
/SEN_100V: C3.1, R1.2, R2.1, U2.J7_66 (ADCINC1)
/SHA: C4.2, Q1.3 (S), Q2.2 (D), U1.18 (SHA), U3.8 (IP+)
/SHB: C5.2, Q3.3 (S), Q4.2 (D), U1.15 (SHB), U4.8 (IP+)
/SHC: C6.2, Q5.3 (S), Q6.2 (D), U1.12 (SHC), U5.8 (IP+)
Fan_Power: J9.1, J10.1, J10.3, J10.5, J11.1, J11.3, J11.5
GND: C1.2, C2.2, C3.2, C7.2, C8.2, C9.2, C10.2, C11.1, C12.1, C13.1, C14.2, C15.2, C16.2, C17.2, C19.2, C20.2, C24.2, C25.2, C27.2, CR4.1 (ADJ/GND), D10.1 (K), D11.1 (K), D12.1 (K), D13.1 (K), D14.1 (K), J6.1, J6.5, J7.1, J10.2, J10.4, J10.6, J11.2, J11.4, J11.6, K1.A2, MP2.1, MP2.2, MP2.3, MP2.4, MP2.5, MP2.6, MP2.7, MP2.8, MP2.9, MP2.10, MP2.11, MP2.12, MP2.13, MP2.14, MP2.15, MP2.16, Q2.3 (S), Q4.3 (S), Q6.3 (S), R2.2, R10.2, R24.2, R25.2, U1.8 (GND), U2.J2_20 (GND_1), U2.J3_22 (GND_1), U2.J6_60 (GND_1), U2.J7_62 (GND_1), U2.J11_3 (GND_1), U2.J11_4 (GND_1), U2.J12_5 (GND_1), U2.J13_5 (GND_1), U2.J14_3 (GND_1), U2.J15_2 (GND_2), U2.JP4_2 (GND_2), U2.JP4_3 (GND_2), U2.JP5_2 (GND_2), U2.JP5_3 (GND_2), U2.JP6_2 (GND_2), U2.JP6_3 (GND_2), U2.JP7_2 (GND_2), U2.JP7_3 (GND_2), U3.2 (GND), U4.2 (GND), U5.2 (GND), U6.4 (-V), U7.3 (GROUND)
unnamed: D10.2 (A), R50.1
unnamed: D11.2 (A), R52.1
unnamed: D12.2 (A), R34.1
unnamed: D13.2 (A), R35.1
unnamed: D14.2 (A), R36.1, R37.1
unnamed: J1.1, K1.A1
unnamed: Q1.1 (G), R3.2
unnamed: Q2.1 (G), R4.2
unnamed: Q3.1 (G), R6.2
unnamed: Q4.1 (G), R5.2
unnamed: Q5.1 (G), R7.2
unnamed: Q6.1 (G), R8.2
unnamed: R33.1, R34.2
unnamed: R49.1, R50.2
unnamed: R51.1, R52.2
unnamed: R22.2, R24.1, U6.3 (+INA)
unnamed: R25.1, R28.1, U6.5 (+INB)
unnamed: R21.2, R23.2, U6.2 (-INA)
unnamed: R26.2, R27.2, U6.6 (-INB)

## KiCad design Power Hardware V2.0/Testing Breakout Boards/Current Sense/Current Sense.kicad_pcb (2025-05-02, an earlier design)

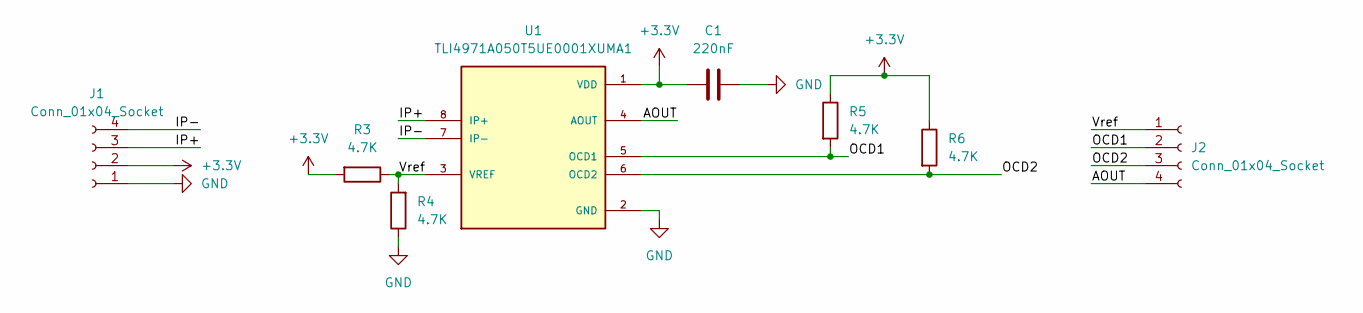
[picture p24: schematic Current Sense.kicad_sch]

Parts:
C1: 220nF; C_0603_1608Metric; Part Number CL21B224KAFNNNE
J1, J2: Conn_01x04_Socket; PinHeader_1x04_P2.54mm_Vertical; Part Number RS1-04-G
R3, R4, R5, R6: 4.7K; R_0805_2012Metric; Part Number CRCW08054K70FKEAC
U1: TLI4971A050T5UE0001XUMA1; PARTREV 1.20

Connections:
+3.3V: C1.1, J1.2, R3.2, R5.1, R6.1, U1.1 (VDD)
/AOUT: J2.4, U1.4 (AOUT)
/IP+: J1.3, U1.8 (IP+)
/IP-: J1.4, U1.7 (IP-)
/OCD1: J2.2, R5.2, U1.5 (OCD1)
/OCD2: J2.3, R6.2, U1.6 (OCD2)
/Vref: J2.1, R3.1, R4.2, U1.3 (VREF)
GND: C1.2, J1.1, R4.1, U1.2 (GND)

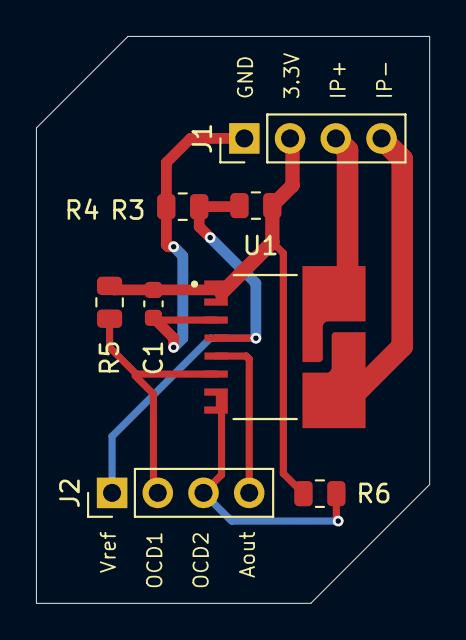
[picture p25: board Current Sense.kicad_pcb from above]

Board: 2 copper layers, 21.8 x 31.5 mm, 8 parts (0 on the bottom side), 8 nets.

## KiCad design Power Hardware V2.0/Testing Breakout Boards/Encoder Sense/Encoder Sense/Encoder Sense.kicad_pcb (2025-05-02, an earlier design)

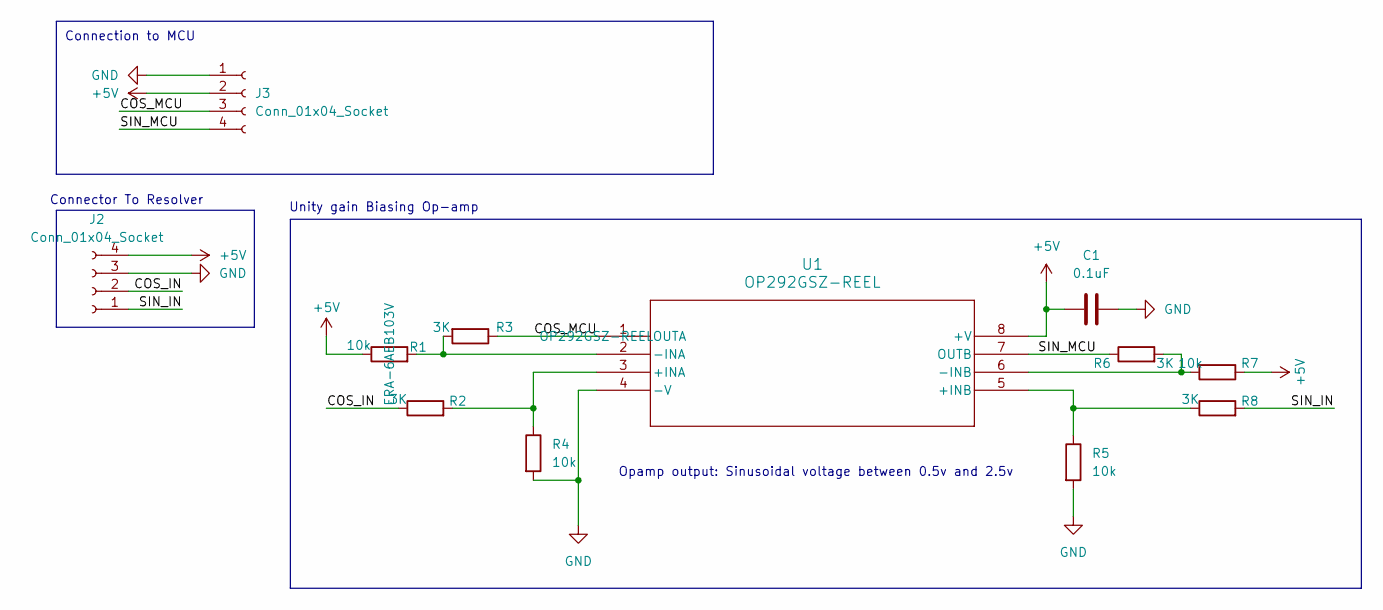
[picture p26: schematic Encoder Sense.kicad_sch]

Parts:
C1: 0.1uF; C_0805_2012Metric; Part Number 0805ZD104KAT2A
J2, J3: Conn_01x04_Socket; PinHeader_1x04_P2.54mm_Vertical; Part Number RS1-04-G
R1, R4, R5, R7: 10k; R_0805_2012Metric; Part Number ERA-6AEB103V
R2, R3, R6, R8: 3K; R_0805_2012Metric; Part Number CRG0805F3K0
U1: OP292GSZ-REEL; R_8_ADI; Part Number OP292GSZ-REEL

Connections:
+5V: C1.1, J2.4, J3.2, R1.1, R7.1, U1.8 (+V)
/COS_IN: J2.2, R2.1
/COS_MCU: J3.3, R3.1, U1.1 (OUTA)
/SIN_IN: J2.1, R8.2
/SIN_MCU: J3.4, R6.1, U1.7 (OUTB)
GND: C1.2, J2.3, J3.1, R4.2, R5.2, U1.4 (-V)
unnamed: R2.2, R4.1, U1.3 (+INA)
unnamed: R5.1, R8.1, U1.5 (+INB)
unnamed: R1.2, R3.2, U1.2 (-INA)
unnamed: R6.2, R7.2, U1.6 (-INB)

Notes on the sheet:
Opamp output: Sinusoidal voltage between 0.5v and 2.5v
Connector To Resolver
Connection to MCU
Unity gain Biasing Op-amp


Board: 2 copper layers, 31.0 x 21.3 mm, 12 parts (0 on the bottom side), 10 nets.

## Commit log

2024-12-09 Revision 1 of control board
    [MCU025B_AltRouting_Misc.SchDoc, MCU025B_Block_Diagram.SchDoc, MCU025B_Connectors.SchDoc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]
2025-02-28 Added Live version of Power hardware KiCAD
    [1-1393210-3.step, 1935161.step, 5002.step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]
2025-03-15 switches instead of relays. Short on half bridge fixed. encoder page made. root page connections fixed
    [100SP1T1B4M2QE.step, 1051640001.stp, 60900213421.stp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]
2025-03-18 Schematic Changes
    -Changed 3.3V regulator to a higher power unit for the sin-cos circuit (from 500mA to 3A)
    -Fixed flipped MOTA,B,C connection to Output Terminal
    - Current Sense IC setup
    - Fuses for Phase current outputs
    [1989764.step, Current sense.kicad_sch, Custom Inverter PCB.kicad_pcb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]
2025-03-28 Updated parts numbers for current sensing
    [Current sense.kicad_sch, Custom Inverter PCB.kicad_sch, Gate_Driver_PowerInputs.kicad_sch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]
2025-03-29 no changes
    no
    [Current sense.kicad_sch, Custom Inverter PCB.kicad_pcb, Gate_Driver_PowerInputs.kicad_sch]
2025-04-13 no major changes
    [Current sense.kicad_sch, Gate_Driver_PowerInputs.kicad_sch, Half_Bridges.kicad_sch]
2025-04-19 Sine-cos test
    [Encoder Input.kicad_sch, Gate_Driver_PowerInputs.kicad_sch]
2025-04-20 Resolver Reading opamps
    [Current sense.kicad_sch, Custom Inverter PCB.kicad_sch, Encoder Input.kicad_sch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]
2025-04-20 EDA models
    EDA models
    [OP292GSZ-REEL.step]
2025-04-20 footprint lib fixes
    [1935161.step, 5002.step, CSD19532Q5B.step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]
2025-04-20 footprint fixes
    [Current sense.kicad_sch, Custom Inverter PCB.kicad_pcb, Gate_Driver_PowerInputs.kicad_sch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]
2025-04-21 Pcb layout and tracing
    changed footprint file for current sense ic
    did layout and tracing for pcb
    created bom
    [Current sense.kicad_sch, Custom Inverter PCB BOM V2.0.csv, Custom Inverter PCB.kicad_pcb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]
2025-04-22 PCB Fixes
    [Custom Inverter PCB.kicad_pcb, Gate_Driver_PowerInputs.kicad_sch, Half_Bridges.kicad_sch]
2025-04-22 Fixed con issue with trace interfering with mosftet HVDC connection
    [Custom Inverter PCB.kicad_pcb]
2025-05-02 breakout boards
    [Current Sense.kicad_pcb, Current Sense.kicad_sch, Encoder Input.kicad_sch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]
2025-05-27 Ver2.1 pushed
    Error fixes:
    -floating plane
    - Unconnected sinecose node
    - Standoff rubbing
    [1-1393210-3.step, 100SP1T1B4M2QE.step, 1051640001.stp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]
2025-05-28 Datasheets into components
    [Current sense.kicad_sch, Encoder Input.kicad_sch, Gate_Driver_PowerInputs.kicad_sch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]
2025-06-22 Added 100-12 and 12-5 regulators added fan headers
    [Custom Inverter PCB.kicad_pcb, Custom Inverter PCB.kicad_sch, Gate_Driver_PowerInputs.kicad_sch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]
2025-06-27 PCB V3 changes
    -HV outputs and inputs changed to screw terminals for lugs
    - Fuses changes to 50A
    - ADC pin for temp sense along with the temp sensing circuit
    - Added more pins to motor encoder term for temp sense
    [1-1393210-3.step, 100SP1T1B4M2QE.step, 1935161.step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]
2025-06-27 PCB layout
    [Current sense.kicad_sch, Custom Inverter PCB.kicad_pcb, Custom Inverter PCB.kicad_sch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]
2025-06-28 V3 layout
    [Encoder Input.kicad_sch]
2025-06-28 V3.0 is ordered
    [Current sense.kicad_sch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]
2025-06-30 V3 push
    [Custom Inverter PCB.kicad_pcb, Encoder Input.kicad_sch, Gate_Driver_PowerInputs.kicad_sch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]
2025-06-30 3D models added
    Added most of the 3D models will add more to complete
    [Custom Inverter PCB.kicad_pcb]
2025-07-02 BOM list
    [Current sense.kicad_sch, Custom Inverter PCB BOM V2.0.csv, Custom Inverter PCB BOM V3.0.csv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]
2025-07-15 3d models
    [Custom Inverter PCB.kicad_pcb]

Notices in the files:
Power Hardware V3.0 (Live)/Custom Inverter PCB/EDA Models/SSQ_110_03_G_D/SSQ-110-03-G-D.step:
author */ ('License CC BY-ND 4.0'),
